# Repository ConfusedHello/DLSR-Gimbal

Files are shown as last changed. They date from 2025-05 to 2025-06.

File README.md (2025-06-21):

# DSLR Gimbal
A DIY 3-axis camera gimbal designed for full frame cameras, built as part of the Hack Club Highway to Hardware program!

As I'm somewhat of a hobbyist photographer, I've considered the idea of building my own camera gimbal for videography as even second-hand on Facebook Marketplace they can be a few hundred AUD. However, I've never particularly had the opportunity (or funds) to attempt it ~~spent all my money on cameras~~.

The gimbal is is powered by iPower's GM5208-24 brushless motors and is constructed primarily from Carbon Fibre sheets/tubes.

<!-- At the time of building, the project cost AU$ , or approx. US$ . -->

For details about the design process, other information, check out the [development journal](highway.hackclub.com/projects/ConfusedHello/DLSR-Gimbal). \*Local copy available in [JOURNAL.md](/JOURNAL.md)

The BOM for the frame is in [/src/frame/README.md](/src/frame/README.md) while the BOM for the PCBs are in [/production/BOM](https://github.com/ConfusedHello/STorM32-NT/). For simplicity, a summary has been provided at the bottom of this document.

## The Frame:
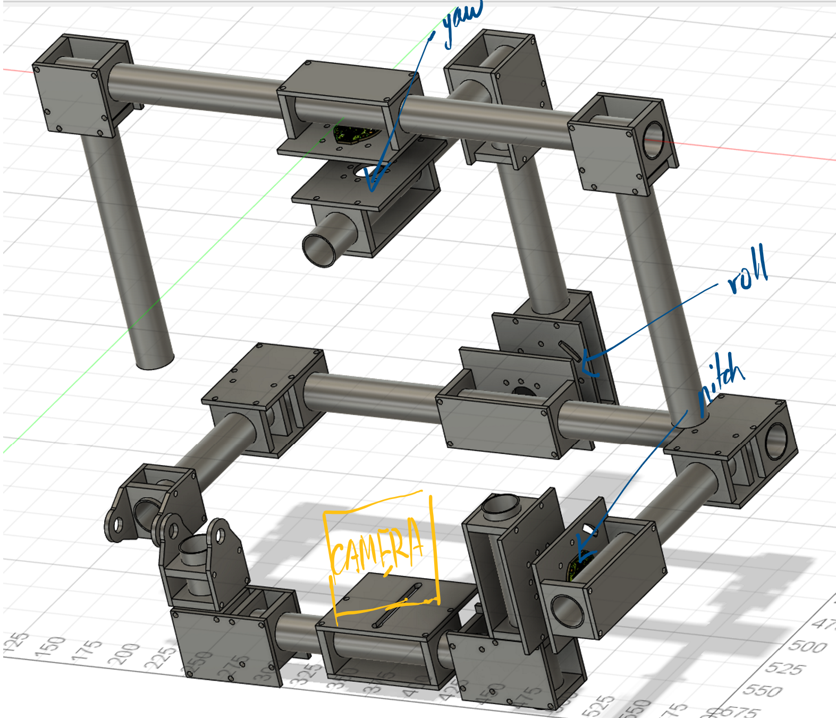
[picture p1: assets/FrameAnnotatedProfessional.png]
Frame
 

## The Controller
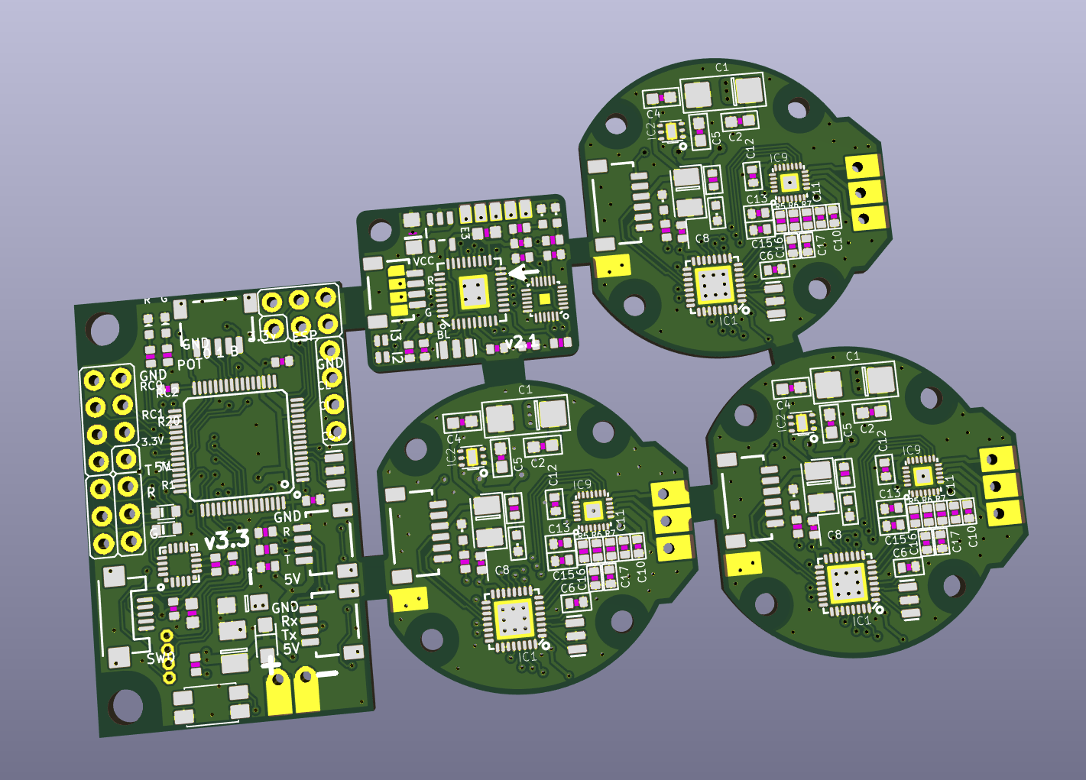
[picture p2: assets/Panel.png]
PCB


## The Setup
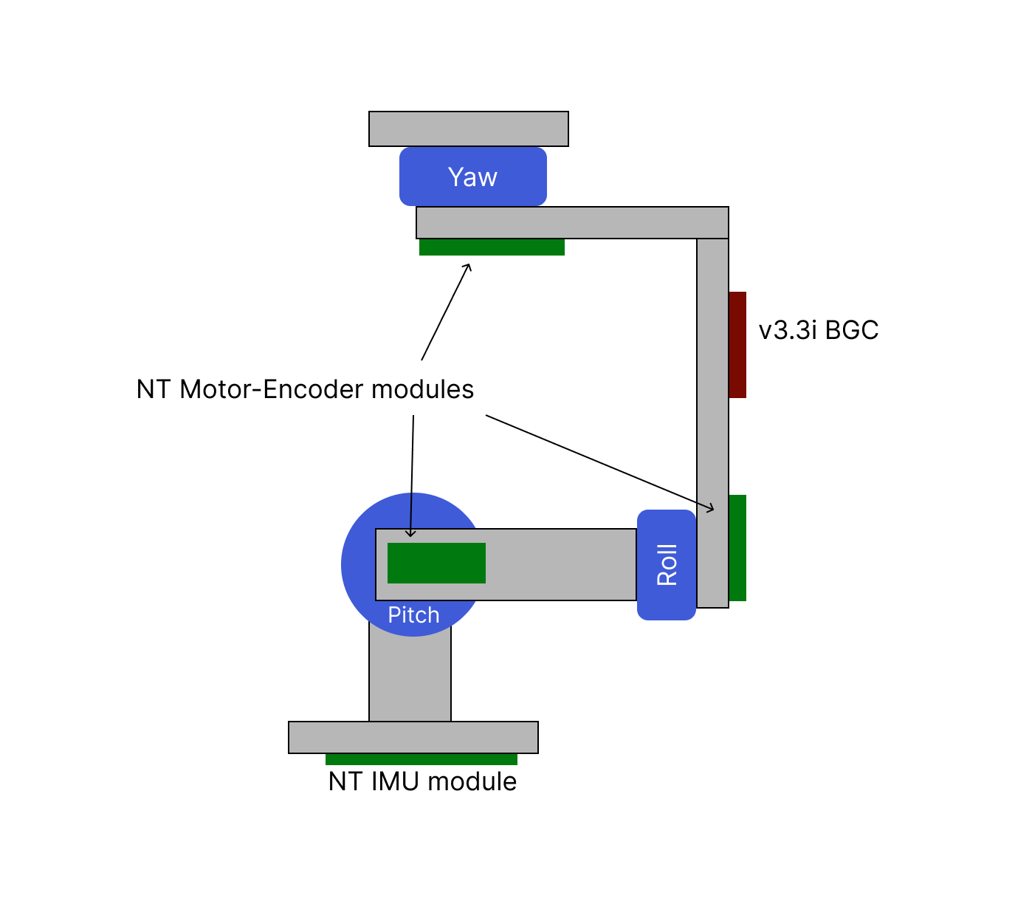
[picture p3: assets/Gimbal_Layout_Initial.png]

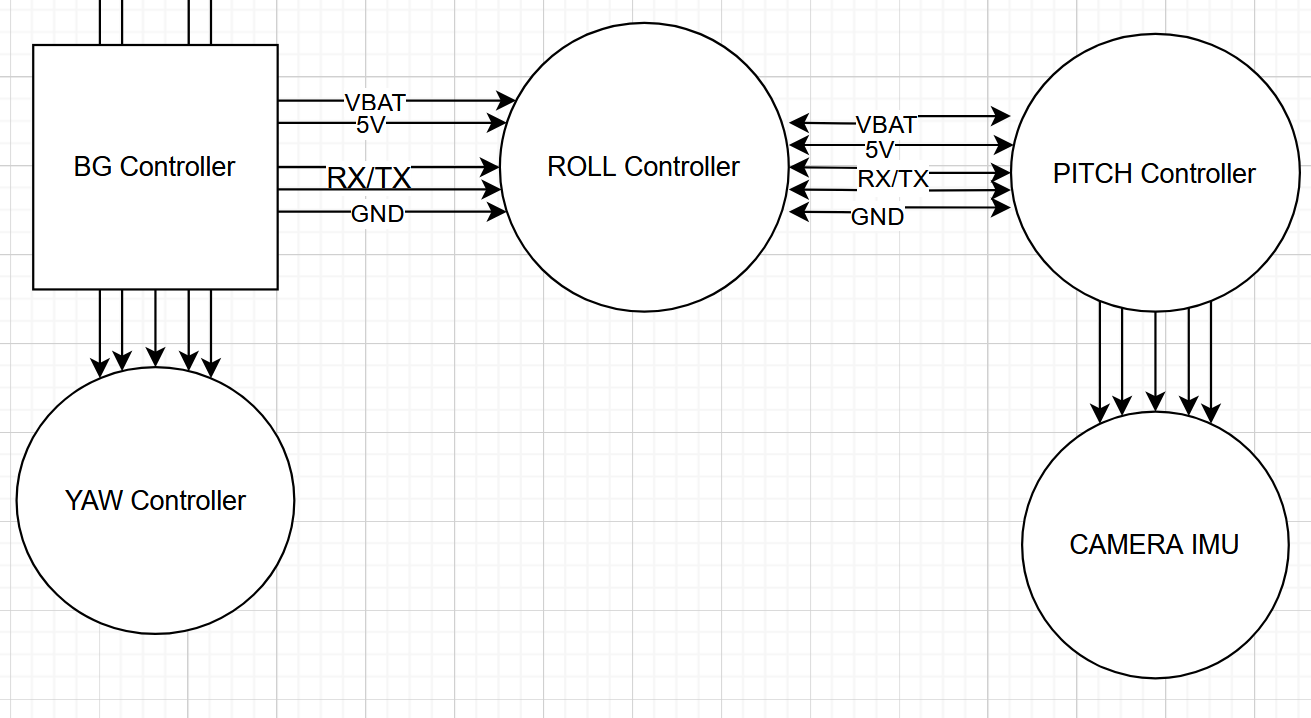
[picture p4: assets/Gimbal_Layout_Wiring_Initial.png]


## BOM
### Frame
| Item Name | Cost (Total) | Amount | Link|
|---|---|---|----|
| GM5208-24 motor | AU$207.75 | 3 | [Aliexpress](https://www.aliexpress.com/item/32900557812.html) |
| 200x300x3mm Carbon Fibre Panel | AU$80.07 | 3 | [Aliexpress](https://www.aliexpress.com/item/1005007049758967.html) |
| 22x20x600mm Carbon Fibre tube (2pc) | AU$60.99 | 2 | [Aliexpress](www.aliexpress.com/item/1005006421809160.html) |
| Aluminium Tube Clamp | AU$74.80 | 44 | [Aliexpress](https://www.aliexpress.com/item/1005001563658390.html) |
| Camera Screw | AU$2.14 | 1 | [Aliexpress](https://www.aliexpress.com/item/1005006636367450.html) |
Total price: AUD$425.75 (approx. USD$276.34)

### PCB and Components
| Item Name | Cost (Total) | Amount | Link |
|---|---|---|---|
| STM32G431KBU3 | $6.9561 | 3 | [https://lcsc.com/product-detail/Microcontrollers-MCU-MPU-SOC_STMicroelectronics-STM32G431KBU3_C1341901.html](https://lcsc.com/product-detail/Microcontrollers-MCU-MPU-SOC_STMicroelectronics-STM32G431KBU3_C1341901.html) |
| STM32F103RCT6 | $1.89 | 1 | [https://lcsc.com/product-detail/Microcontrollers-MCU-MPU-SOC_STMicroelectronics-STM32F103RCT6_C8323.html](https://lcsc.com/product-detail/Microcontrollers-MCU-MPU-SOC_STMicroelectronics-STM32F103RCT6_C8323.html) |
| STM32F103T8U6 | $3.16 | 1 | [https://lcsc.com/product-detail/Microcontrollers-MCU-MPU-SOC_STMicroelectronics-STM32F103T8U6_C19671.html](https://lcsc.com/product-detail/Microcontrollers-MCU-MPU-SOC_STMicroelectronics-STM32F103T8U6_C19671.html) |
| Misc. Components (Resistors, Capacitors, Sockets, IMU, V-reg) | ~$40 | | |
|PCB	|A$3.08	|1	||
|Stencil	|A$10.77|	1	||
| Shipping	|A$26.21|	1||

Combined total for the project:
AUD$425.75 + USD$25.97 + USD$52
= approx. USD$326.12

<hr>

Made with ❤️ by [@ConfusedHello](https://github.com/confusedhello)

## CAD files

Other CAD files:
src/frame/Components/22mm_Tube_Clamp.f3d
src/frame/Components/Camera_Mount.f3z
src/frame/Components/Handle_Joint.f3z
src/frame/Components/Pitch_Bearing_Mount.f3z
src/frame/Components/Pitch_Bearing_Mount_Save.f3z
src/frame/Components/Tube_Joint.f3z
src/frame/Components/Tube_Joint_Save.f3z

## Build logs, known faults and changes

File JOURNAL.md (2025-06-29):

---
title: "DLSR Gimbal"
author: "ConfusedHello"
description: "A DIY Gimbal for a Full Frame Camera!"
created_at: "2025-05-26"
---

**Total time spent to date: 60hrs**

## June 18th - Final Design Update
Hello again - it's been a while. I've been focusing on my other project, [USB-Mic](https://highway.hackclub.com/projects/ConfusedHello/USB-Mic) recently - then I was sick for a week. Then there was the state-wide GAT (the memes are crazy).

Anyways, for the final journal entry for the design, I present: THE PANEL
PCB. I will be submitting this today!

It's been a crazy last few weeks working on this project - looking forward to (hopefully) building it soon!

**Time spent: 8hrs**

## June 5th to June 9th - Final Prep
A few things these last few days! Did most of the final prep for submission last Friday and today. Had the zoom call as well a few days ago! Continued working on the BOM on LCSC for the PCBs. Also look there's a [README](https://github.com/ConfusedHello/DLSR-Gimbal/) now!

I've also been panelising all the PCBS (3x motor controllers, a BGC and a IMU module) into a 60mmx100mm panel (I swear this is taking ages) so I don't have to pay for 5 seperate JLC orders. PCBA is also out of the question as the amount of time it would take to properly set up all the footprints would be crazy, so I'm grabbing a stencil from JLC and will be attempting to soldier the board with a hot air rework station at school.

I feel like the finish line is close - just a few more days to finish off the panel!

**Time spent: 10hrs**

## June 4th - Git merge
Spent some time searching for the components for the PCBs as well as a few other misc. components (phone mount for display, LiPo etc.) The completed BOM will be available in the [README](https://github.com/ConfusedHello/DLSR-Gimbal/).

**Time spent: 3hrs**

## June 3rd ...
**Time spent: 2hrs**

## June 2nd - Git branch
Well today was one heck of a day! Frame is done, and it's [BOM](https://github.com/ConfusedHello/DLSR-Gimbal/blob/main/src/frame) has been roughed out! Tommorrow I'll most likely spend a little bit of time on the PCB BOMs but I don't expect too much time to go into it. Now behold, the completed frame in all it's non-rendered glory!

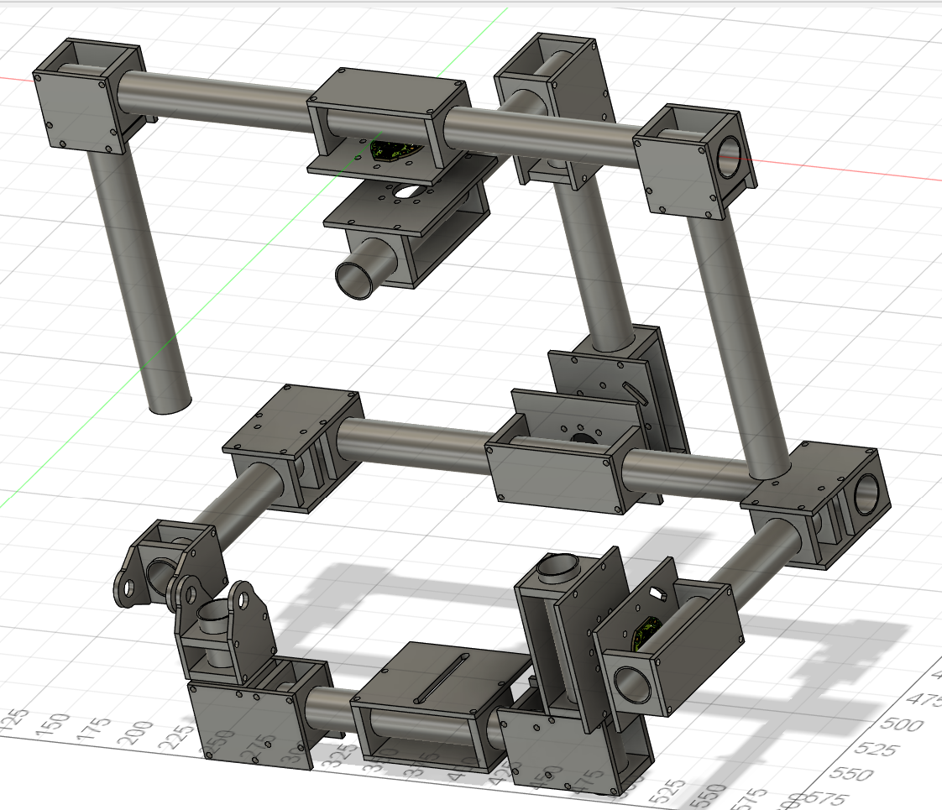
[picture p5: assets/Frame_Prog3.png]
Image of the completed gimbal frame


Just one issue however. When I started building the project, the clamps I found (literally only one listing on Aliexpress) were apparently $1.5 each (I even added them to cart and went to pay just to check). Unfortunatly they're now listed at $7.50 for 2??? Meaning I need about $160AUD of clamps?

Update from later: found 1 other listing for 1.7AUD for one? Totals to $74.8 - a lot more reasonable. PCB work continues tomorrow!

**Time spent: 5hrs**

## June 1st - Git push
Happy April fools! Wait no it's June... Anyways, Started off today by redoing the base mounts for the motors, I decided the double-clamp was a bit excessive even if I erred on the side of caution. I also realised, the 90° could also be easily accomplished using the same method as the motor mounts! So, after a few hours of work - the gimbal modeling is yet another step closer to being done! Also spent some time sanity-checking some carbon fibre panel/tube prices while I was at it. 

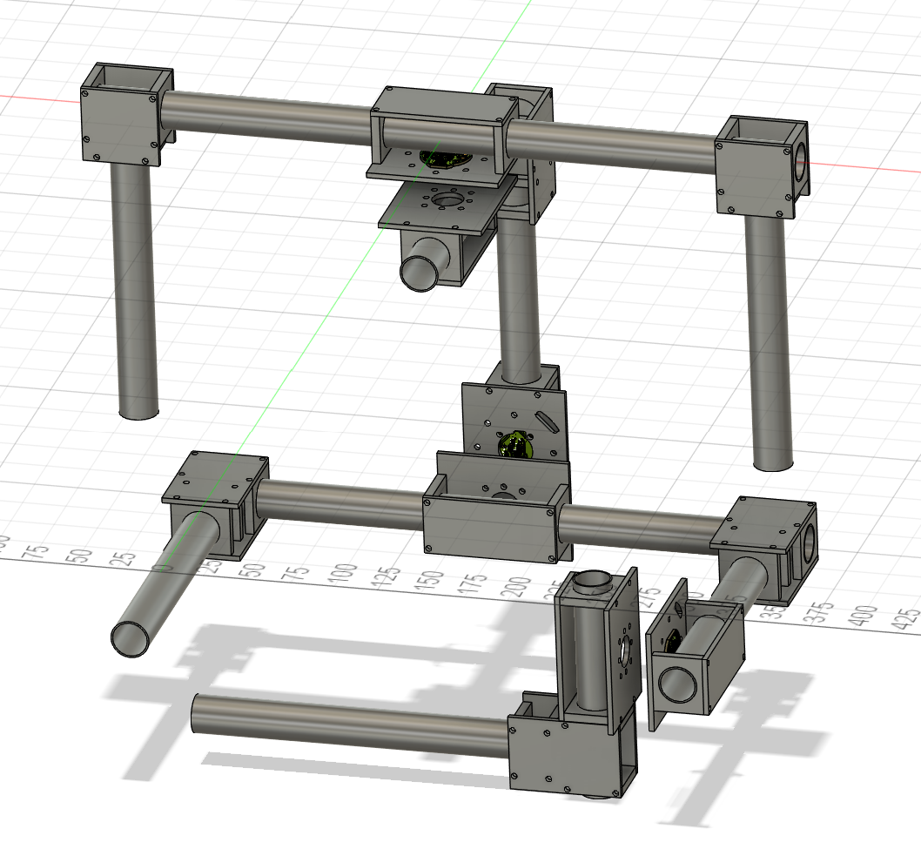
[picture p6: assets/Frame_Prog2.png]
Unfinished gimbal 3d model


Tomorrow will focus on the camera mouting plate (should be pretty easy) and the joint for the other side (still don't know how that'll work to be honest). In the coming days I'm planning on finalising the PCBs as well as confirming a BOM + price. Project is over going pretty well and *[I'm feeling good](https://youtu.be/oHRNrgDIJfo?t=40)!*

**Time spent: 5hrs**

## May 31st...
Worked on some modelling and re-thought the 90° joints. Will elaborate tomorrow.

**Time spent: 2hrs**

## May 30th - Git commit
So much designing today! Started off by creating a quick reference model for the tube clamp I managed to find.

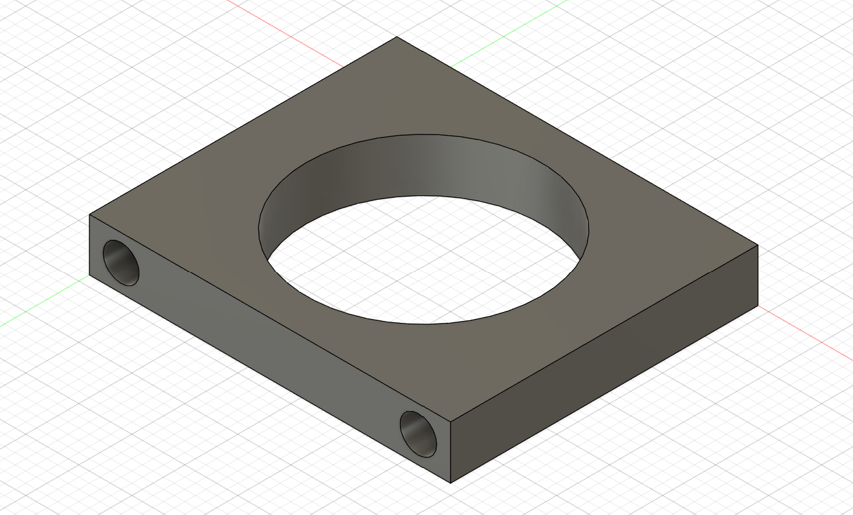
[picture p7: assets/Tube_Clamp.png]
Tube clamp 3d model


Next I moved onto a mount for the motors, here's where I realised that the motor controller modules that were designed with the in-built encoder in mind had non-optimal placement of the plug - it was on the side of the board with the encoder. So it's time for some KiCad-ing! Here's the end result of the motor controller / encoder PCB.

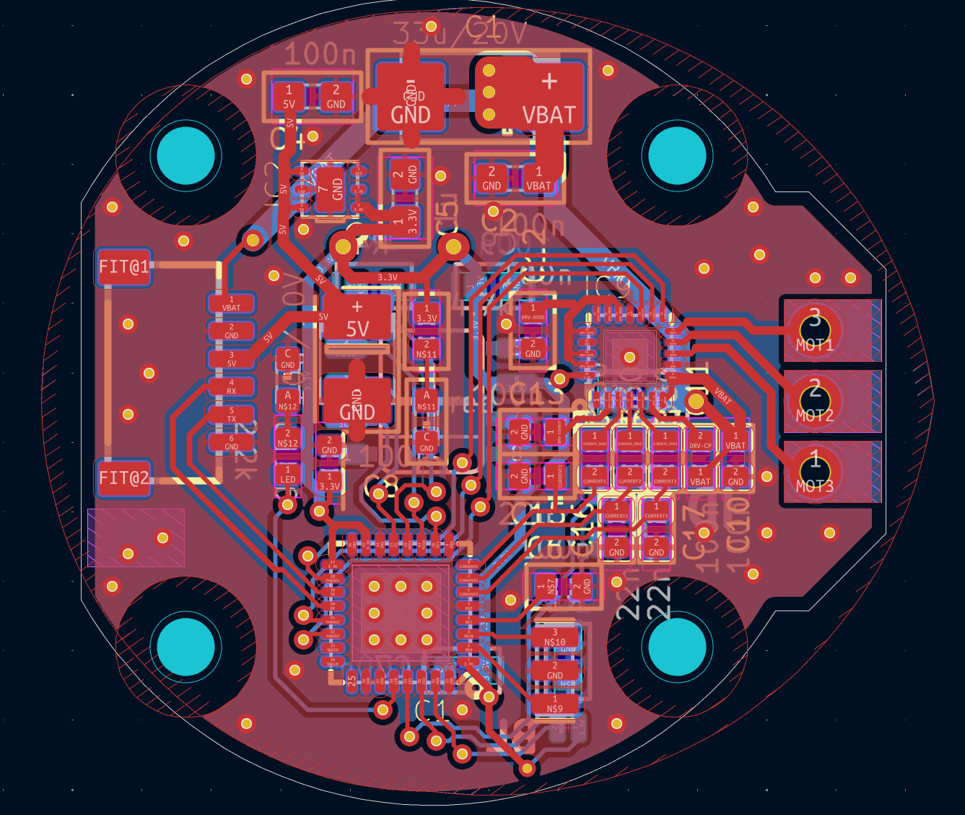
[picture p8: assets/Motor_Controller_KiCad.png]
Image of Motor controller PCB

*More details on these boards can be found in my repo [here](https://github.com/ConfusedHello/STorM32-NT/tree/main/modules/Motor).*

My next job was finishing up the design for the motor mount in Fusion360. The plates will be cut from a 3mm sheet of Carbon Fibre, allowing for a perfect distace between the magnet and the encoder (0.5-3mm).

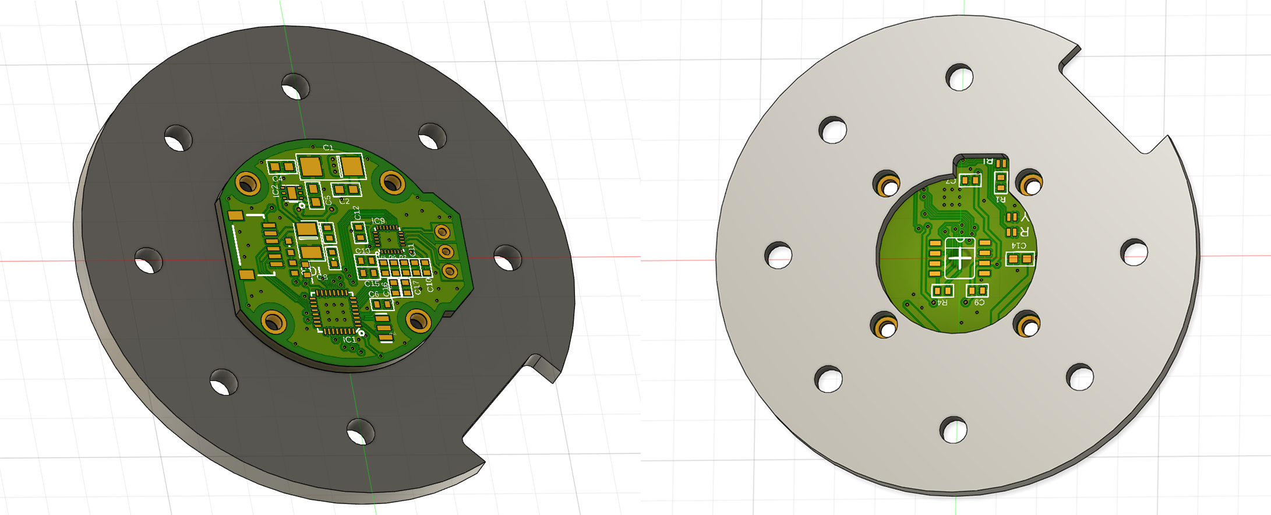
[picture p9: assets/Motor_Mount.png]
Image of mount for the Motor controller PCB


Nice! Now we have the basic component for mounting our motors to! Next, let's work on the mounting plate for the *other* side of the motor (the side that spins) and start putting a few things together!

After designing a mount for both sides of the yaw motor, let's try having a quick look at what we're up to.

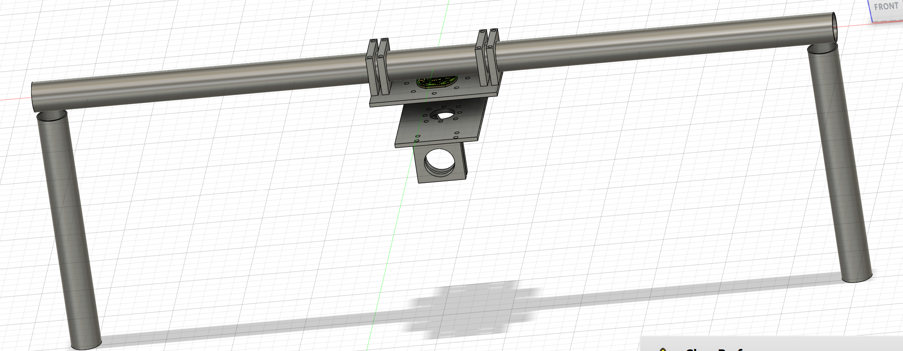
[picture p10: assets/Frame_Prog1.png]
Image of gimbal handle


Not bad for the day! Tomorrow will focus on continuing to build on the gimbal design,as well as the camera mount + IMU.

**Time spent: 10hrs**

## May 29th - Git add
Finally ready to move onto some designing! After some more research I landed on the GM5208-12/24 motor. It's the standard motor from iPower's GM5 lineup, albiet not particularly cheap at approx $60AUD each ($38.66USD) it's the lineup made for gimbals and suits the job well. I'll add these to the newly-made [BOM](https://github.com/ConfusedHello/DLSR-Gimbal/blob/main/src/frame).

After a quick search online, I was able to find the dimensions for the motor online.

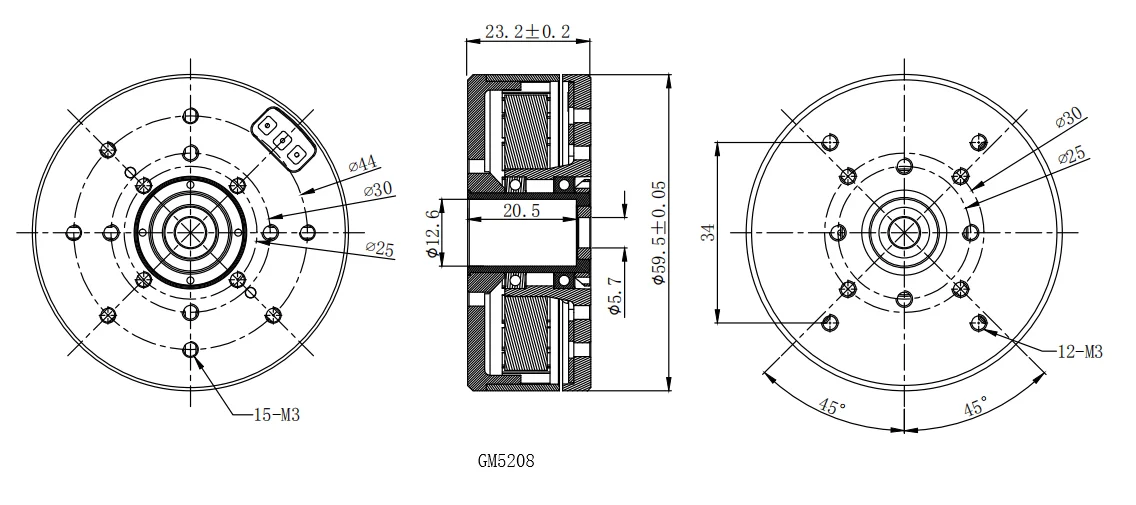
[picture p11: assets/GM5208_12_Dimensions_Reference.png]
Image of the dimensions of the GM5208 gimbal motor


Next I deep-dived into the [STorM32 BGC project](https://github.com/olliw42/storm32bgc/), after looking through the documentation as well as the schematics of the components I settled on the T-STorM32 architecture and created the first draft of the gimbal layout and how it would be wired up.

Draft of the gimbal design with labled components

Draft of the gimbal wiring

After some more planning for how the motor controllers would be mounted...

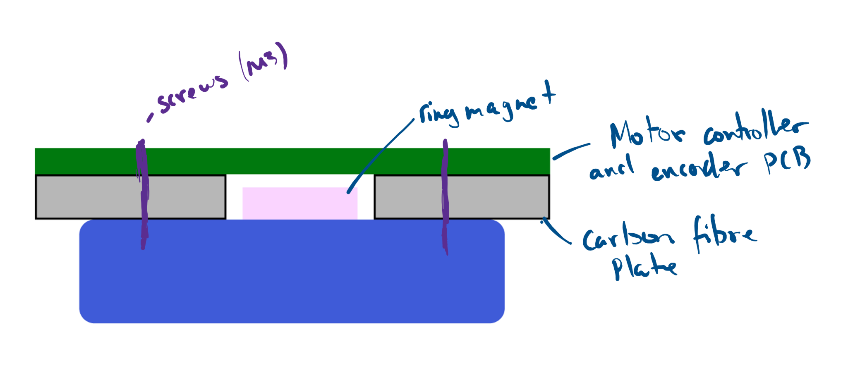
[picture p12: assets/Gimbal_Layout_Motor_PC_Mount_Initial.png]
Draft of the motor controller mount


And for some quick ideas:
- CF tubes instead of plates = cheaper
- 90° joins using cut CF plates and screws
- custom joystick + button pcb/mount

**Time spent: 6hrs**

## May 28th - Git fetch
Spent most of today finishing off my hackpad. However, in the hour and a bit I spent today researching, there was a big discovery. The STorM32 project, a 2013 gimbal board designed... for drones. After some extensive research, I only found 2 examples of this board being used for a full-frame camera gimbal. The good news? It's **open source**, meaning I now have an excellent foundation to build upon for the controller side.

I now have the confidence to begin designing the frame, tommorrow I will begin by choosing a motor, then looking into designing an encoder PCB/frame for it.

**Time spent: 2hrs**

## May 27th - Git clone
A lot more research research on existing DIY Camera Gimbals today! The main takeaway is that the manjority are actually **two-handle gimbals**. Why is that?

Once you've moved from light cameras such as a phone or action camera, they're a little difficult to hold in one hand, particularly if they're balanced *above* the level your hands are at (you can think of this like trying to hold a metal pole at a 45° angle in front of your body). Now when you switch to not only being able to hold it directly *below* your hand-level, as well as using *two* hands, it's a whole lot easier.

Spent today looking at basically all the existing DIY gimbals and their components, in summary:
- For non-action camera gimbals, two-handle is the way to go
- The MCU/ESC board that most projects use, the SBG32 (or an older version) are MUCH too expensive (approx. $300 AUD for one), so I'll have to design my own.

Will begin component selection (primarily the motors to use, as well as what the frame will be made of) tommorow to decide on the requirements for the MCU/ESC. This should be slightly easier than going at it with no experience due to some prior experience designing drones.

I'll also use this time to note, the name of the project isn't exactly accurate as I'm designing this for a mirrorless camera... Full Frame Camera Gimbal or something of the sort may have been a more accurate name. Looking forward to tomorrow!

**Time spent: 3hrs**

## May 26th - Init
Today was primarily determining the viability and establishing the general idea for the project.

As I'm somewhat of a hobbyist photographer, I've considered the idea of building my own camera gimbal for videography as even second-hand on Facebook Marketplace they can be a few hundred AUD. However, I've never particularly had the opportunity (or funds) to attempt it ~~spent all my money on cameras~~.

After some debate and sanity-checking my knowledge of a few DJI gimbals, we can now categorize the majority of consumer camera gimbals as either **single-handle handheld gimbals** or **two-handle handheld gimbals**. Images below, respectively.

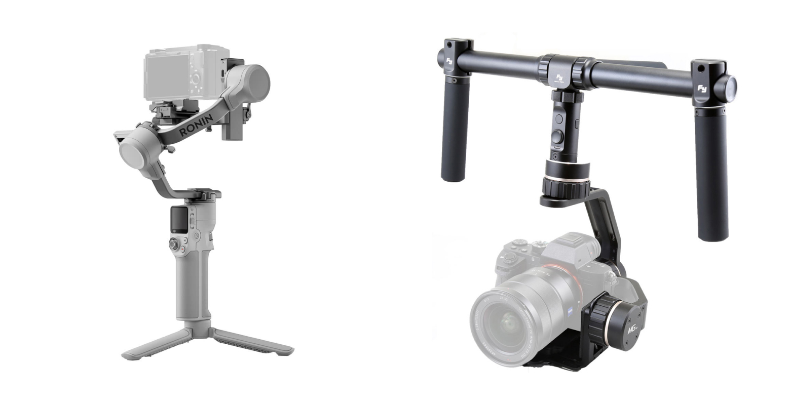
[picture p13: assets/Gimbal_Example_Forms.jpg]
Image with showing two different types of camera gimbals


Now an observant individual may have realised both these form factors have one thing in common. They both stabilise the camera with 3 axis - **pitch**, **roll**, and **yaw**. Diagram by Horia Ionescu.

Diagram of 6 Degrees of Freedom

So while single-handle gimbals are easier to use for phones and your standard cameras (such as the Ronin S supporting up to 3.6kg), you'll never see one on a film set where wheeled steadi-cams, sholder rigs, and other massive gimbals are used.

So what do I actually need? (Hint: this is where we establish our *scope*) Personally, my camera setup without a cage weighs approximatly 1.2kg, well under the Ronin S' 3.6kg limit or the Ronin 4 Mini's 2kg limit - so a single-handle gimbal should do fine. We'll need it to handle somewhere around 2kg, so let's set that as our target.

To summarise:
- I will be designing a 3-axis, single-handle handheld gimbal
- The gimbal must support up to 2kg

Tomorrow's journal will probably not be as detailed as this one, definitely spent too long on it.

**Time spent: 4hrs**

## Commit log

2025-05-30 Create tube clamp component
    [22mm_Tube_Clamp.f3d]
2025-05-30 Update STorM32-NT
    - Added template BGC
    - Uploaded motor controller
2025-05-30 Upload frame design files
    [Motor_Mount_LIVE.f3d]
2025-06-01 Update frame 3d models
    [Handle_Joint.f3z, Motor_Mount_LIVE.f3d, Tube_Joint.f3z]
2025-06-02 Update Gimbal Frame
    [Camera_Mount.f3z, Pitch_Bearing_Mount.f3z, Pitch_Bearing_Mount_Save.f3z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]
2025-06-04 Fix BOM for frame
